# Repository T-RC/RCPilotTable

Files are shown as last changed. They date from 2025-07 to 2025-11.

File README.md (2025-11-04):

# RC Pilot Table
:airplane: This is a height adjustable, auto leveling table, intended for RC pilots. This table uses four [linear actuators](https://www.amazon.com/dp/B00NM8H67C/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) as legs.

:wheelchair: No crossmembers and a shallow deck make it usable for all pilots, including those using a wheelchair. 

:wrench: The table height adjusts simply via a rocker switch. It levels itself via a pushbutton. It is designed for outdoor use and runs on 2S-8S battery power.



## comments, questions and chat
You can leave comments, reviews, ask questions or start a conversation about this project [here](https://github.com/T-RC/RCPilotTable/discussions).

## Project background

Initially, I did not see an issue with the tables at my local AMA field. They are a common design, made of affordable materials and mostly construction wood. 



I believe the design is, at least in parts, inspired by prior art as featured [here](https://www.modelaviation.com/Club-Field-Safety-Benches).

One day, a fellow pilot pointed out that these tables are difficult for him to use. I realized that any table that has crossmembers connecting the legs is inaccessible for a pilot who uses a wheelchair. He also explained that a higher working surface would be nice to have. A few days later, I learned from another club member that a lower table surface would be better suited for his needs. I realized that a better table has to be height adjustable.
A web search for an off-the-shelf solution yielded no convincing options and neither did my search for better open source designs. I decided to come up with my own solution.

I chose to use [linear actuators](https://www.amazon.com/dp/B00NM8H67C/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) for the height adjustable legs. The rest of the design is driven by this decision. The actuators are marketed for use with solar panels, so they are weather resistant, IP54 rated, and affordable enough at around ~$50 a piece. They are however also not very precise, consistent or repeatable in their positioning and additional electronics are required for a level surface and to prevent rocking.

## The prototype
I have built one prototype so far. After it was finished, I donated it to the [Triple Creek Radio Control Aircraft Club](https://www.triplecreekrc.com) [(facebook)](https://www.facebook.com/share/1CnncBL3pf/?mibextid=wwXIfr) where it is in use since July 2025. The Tripple Creek RC field is located at 12705 Balm Boyette Rd
Riverview, FL 33579. 



## How to operate
Safety first: This is still a prototype. Stay clear of moving parts and use it at your own risk. Only plug in a battery while using it and be ready to unplug if anything unexpected happens. Don't leave a battery plugged in unattended.



The table has an internal 8-36V buck/boost power regulator, so it can handle anything from 2S to 8S battery. Simply plug your pack into the XT60 connector. I don't have exact numbers on the current draw, but obviously it will be higher for lower voltage packs. Very small 2S or 3S packs might not have enough punch.

Use the rocker switch to adjust the deck to the desired height, or slightly below it. Then use the leveling push-button and watch the magic happen. The table will attempt to raise the corners until the deck is level. Leveling happens upwards, so it's best to start below the desired height. The software code will time out after a few seconds, press the button again as needed. The programming is not very sophisticated yet. Press down on a corner and level it again if the table teeters.   

## How to build
A detailed build guide or a build video will follow if there is interest in it [(feel free to leave a comment here)](https://github.com/T-RC/RCPilotTable/discussions). For the time being, I an providing the [FreeCAD](https://www.freecad.org/) drawings, electrical schematics and STLs in the [subfolders](/drawings%20and%20images). I have video of the build of the electrical box. Github does not allow me to post it here, but I can make it available on request.

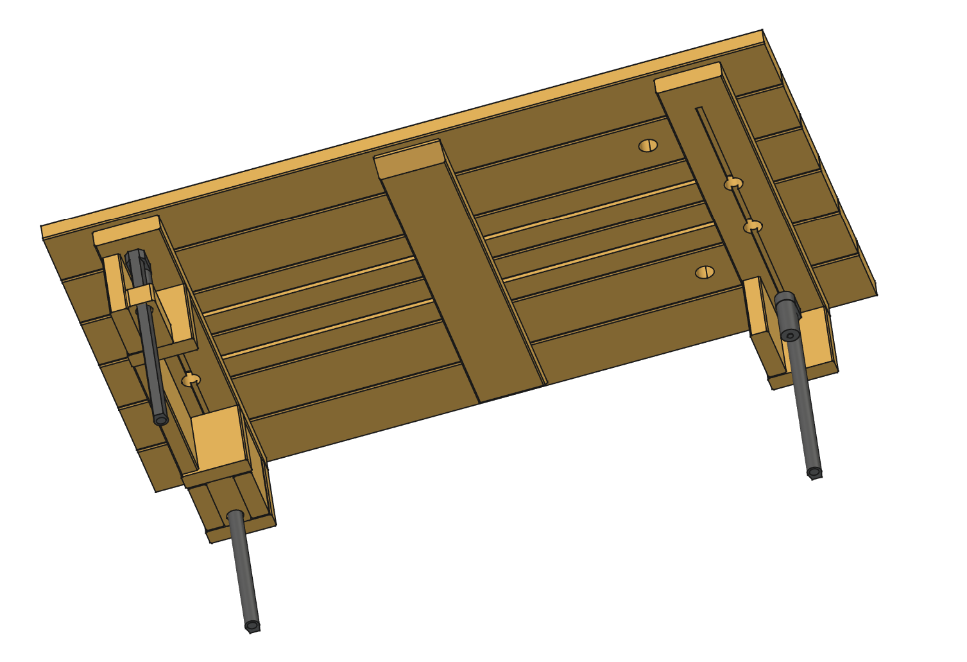
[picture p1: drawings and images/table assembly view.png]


### Lumber
I chose to only use one kind of timber for the entire build. This reduces waste and makes purchasing easier for us hobbyists. 2 in. x 6 in. dimensional lumber is readily available at hardware stores and local lumber yards. I built the first prototype from green western red cedar, but any hardwood or SPF will work the same depending on climate and weather, how long you want your table to last, how good you want it to look and how much $ you're willing to spend.

You need a total of approximately 50ft:

| count | length | use
| --- | --- | ----
| 6 pcs | 60" | for deck
| 3 pcs | 32" | for deck support
| 2 pcs | 15" | for side boards (optional, need to be fitted)
| 16 pcs| 6" | for the leg housing sides
| 4 pcs | 2"  | for the leg housing bottoms, use jig to cut

### Legs - linear actuators
The legs I used are [linear actuators](https://www.amazon.com/dp/B00NM8H67C/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) from Amazon.
### 3D Prints
I used [FreeCad](https://www.freecad.org/) for all the designs and [all drawings are here](/drawings%20and%20images). The STLs are posted [here](/3D%20print%20STLs). As filament, I am using either [Polymaker ASA](https://www.amazon.com/dp/B09DKQK318/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) or [Priline TPU](https://www.amazon.com/dp/B0BJ5XRDFB/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). 
### electrical box
I chose 3D-printing the box because I can skip several work steps and iterate faster this way. It also allows having a two colored front plate by stopping the printer and changing color after a few layers. An [off the shelve electrical enclosure](https://www.amazon.com/dp/B08N1DD5WJ/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) will work just as well though. As mentioned above, a build video is available.
### feet
The feet are 3D-printed in TPU at 100% infill.
### vertical wing restraint hanger
The vertical wing restraint is a removable design made from PVC pipe (not my idea, who get's credit?). It can be inserted into holes on the table to provide a hard stop for fixed-wing aircraft during setup and testing. Since these are not needed all the time, the restraints are removable and I designed a simple hanger to stow them when not in use.
The hanger is 3D-printed in ASA. I'm sure there is an injection molded substitute somewhere, but I couldn't find anything I liked so I designed my own.

### router template
This 3D-print is used as a jig to help cutting the bottom of the leg housing. The linear actuator has to be tightly held or else the table would get wiggly. Use [this template](/3D%20print%20STLs/Router%20template.stl) to hold and cut the wooden brackets.

### Amazon - what I bought
These are not affiliate links and I am not trying to monetize or profit of this project. Please also don't consider these reviews or recommendations. The Amazon link below simply takes you to a list of all the stuff that I personally bought and used during the build. It is not a comprehensive list either, but I think it might be helpful nevertheless.  

[Amazon list](https://www.amazon.com/hz/wishlist/ls/PGYE4HTR4F8?ref_=wl_share)

## What's next
- A full build video
- The software can still use some work.
  
let me know what you think [here](https://github.com/T-RC/RCPilotTable/discussions)

## See the prototype or learn to fly RC at Triple Creek RC
[website](https://www.triplecreekrc.com) 

[facebook](https://www.facebook.com/share/1CnncBL3pf/?mibextid=wwXIfr)

## License
Unless otherwise noted, this work is licensed under a
[Creative Commons Attribution 4.0 International License][cc-by].

[][cc-by]

[cc-by]: http://creativecommons.org/licenses/by/4.0/
[cc-by-image]: https://i.creativecommons.org/l/by/4.0/88x31.png
[cc-by-shield]: https://img.shields.io/badge/License-CC%20BY%204.0-lightgrey.svg

[][cc-by]

[cc-by]: http://creativecommons.org/licenses/by/4.0/
[cc-by-image]: https://i.creativecommons.org/l/by/4.0/88x31.png
[cc-by-shield]: https://img.shields.io/badge/License-CC%20BY%204.0-lightgrey.svg

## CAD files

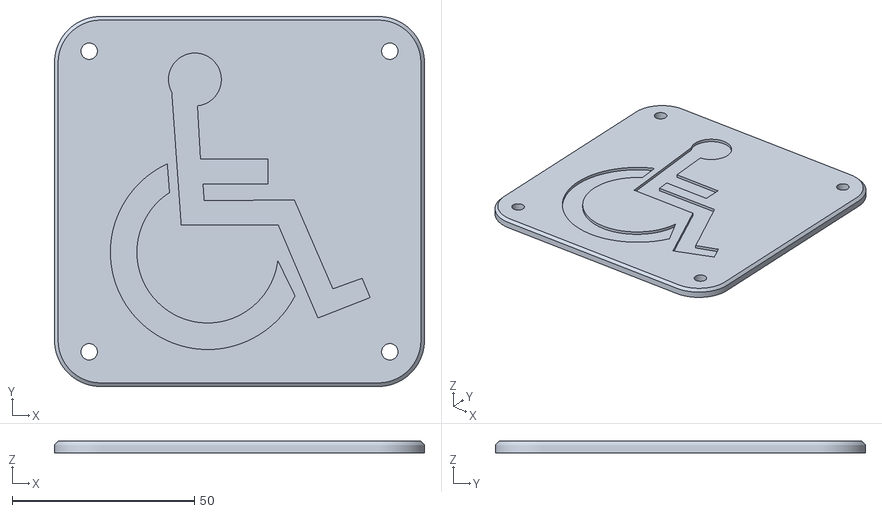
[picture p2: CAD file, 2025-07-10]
3D print STLs/disability sign.stl
101.6 x 101.6 x 3.17

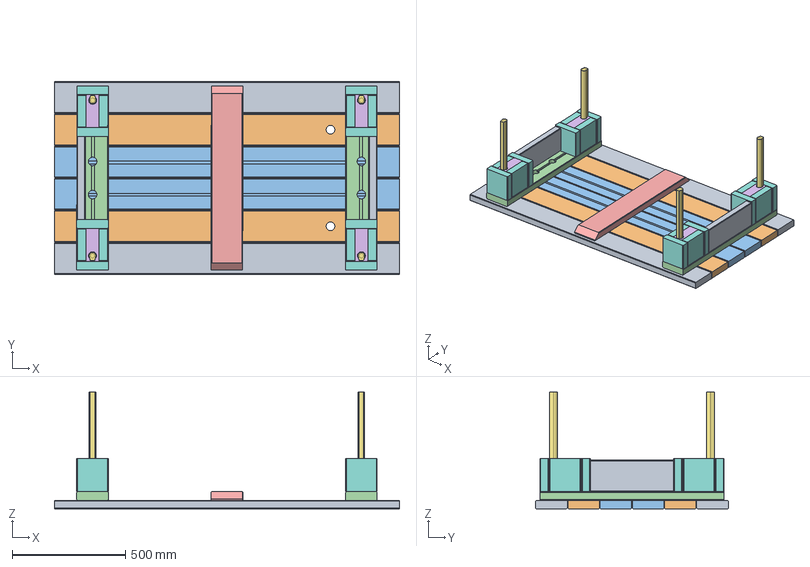
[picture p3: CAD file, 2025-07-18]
drawings and images/pilot table 037.FCStd
1524.0 x 851.4 x 516.3 mm
2x6 60" Deck x 2
2x6 60" Deck with holes x 2
2x6 60" Deck with groove x 2
2x6 32" SubDeck x 2
2x6 32" center SubDeck
2x6 scrap actuator adapter x 4
linear actuator body x 4
2x6 6" Leg x 16
2x6 15" sideboard x 2

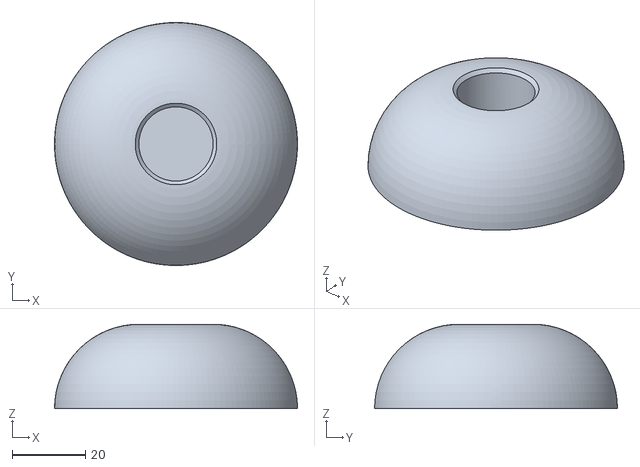
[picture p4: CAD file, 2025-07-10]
3D print STLs/pilot table foot.stl
66.2 x 66.2 x 23.0

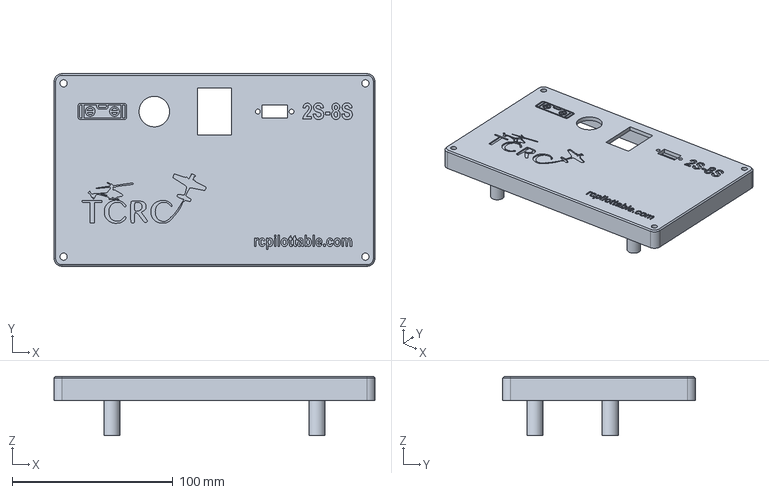
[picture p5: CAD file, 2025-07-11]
drawings and images/e-box 022.FCStd
200.0 x 120.0 x 37.0 mm

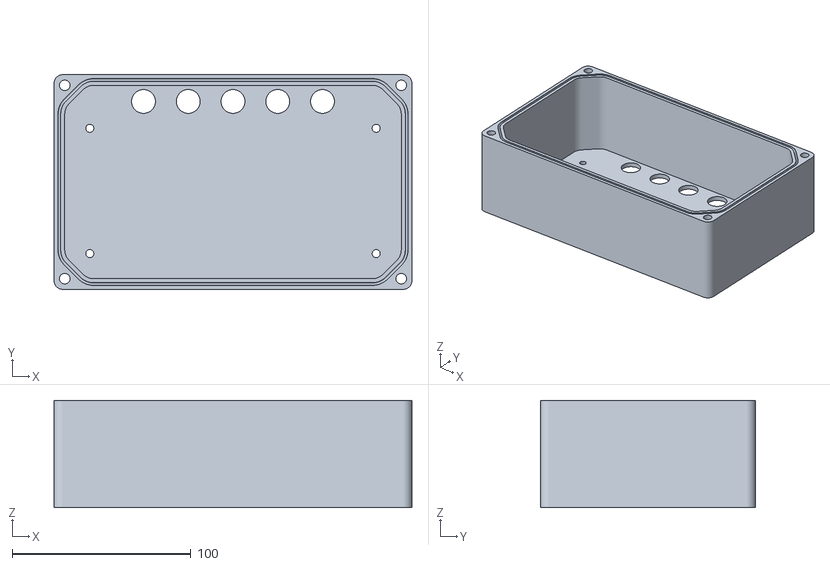
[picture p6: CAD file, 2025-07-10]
3D print STLs/e-box base.stl
200.0 x 120.0 x 60.0

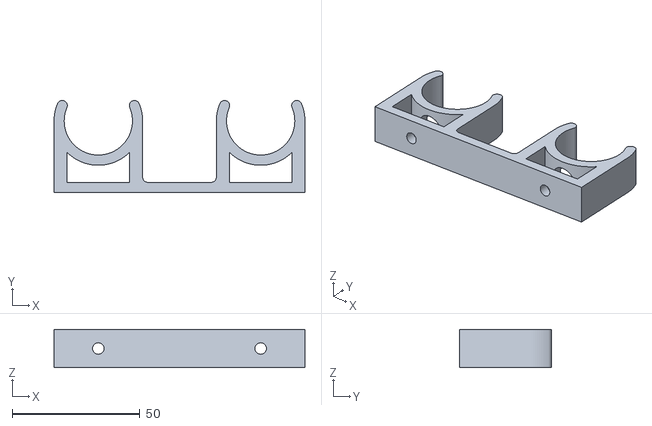
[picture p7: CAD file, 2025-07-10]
3D print STLs/PVC pipe stopper hanger.stl
98.2 x 36.0 x 15.0

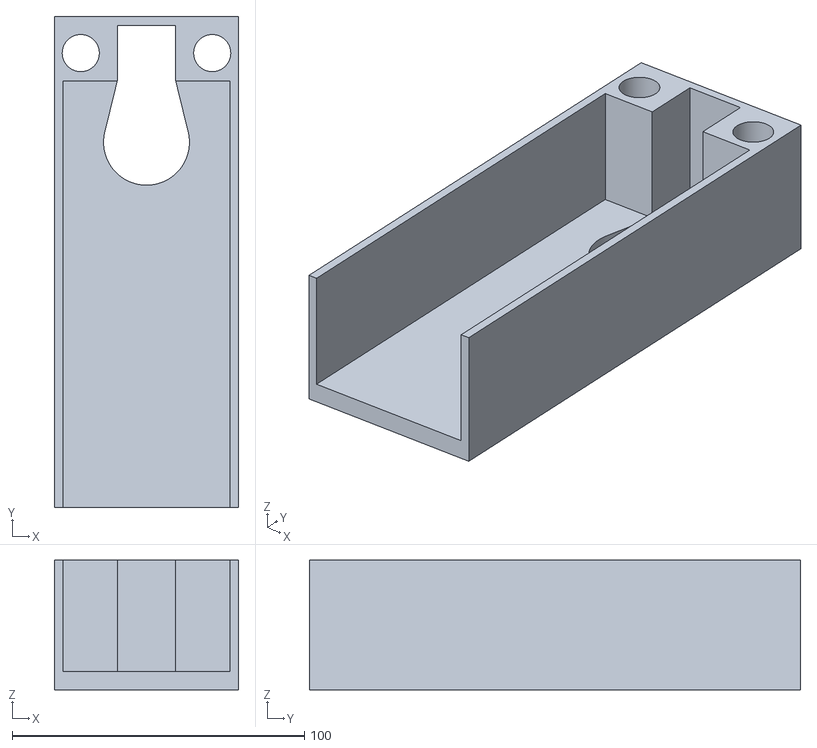
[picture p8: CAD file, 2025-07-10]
3D print STLs/Router template.stl
63.2 x 168.1 x 44.5

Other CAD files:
3D print STLs/e-box lid.stl

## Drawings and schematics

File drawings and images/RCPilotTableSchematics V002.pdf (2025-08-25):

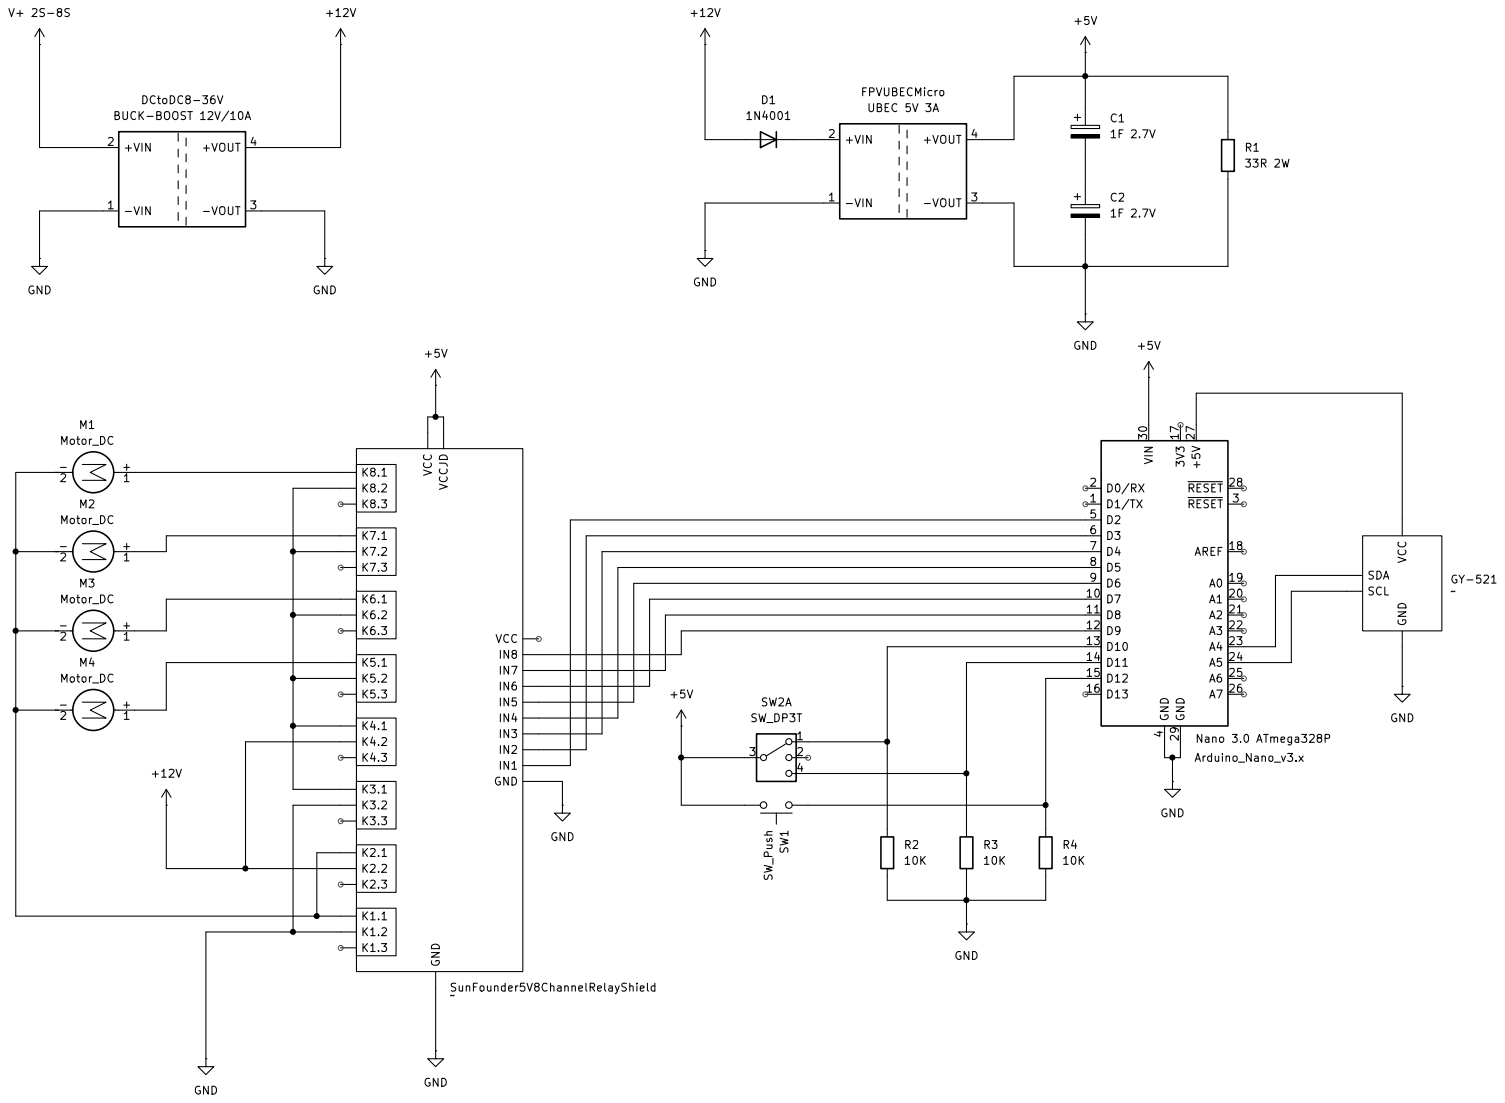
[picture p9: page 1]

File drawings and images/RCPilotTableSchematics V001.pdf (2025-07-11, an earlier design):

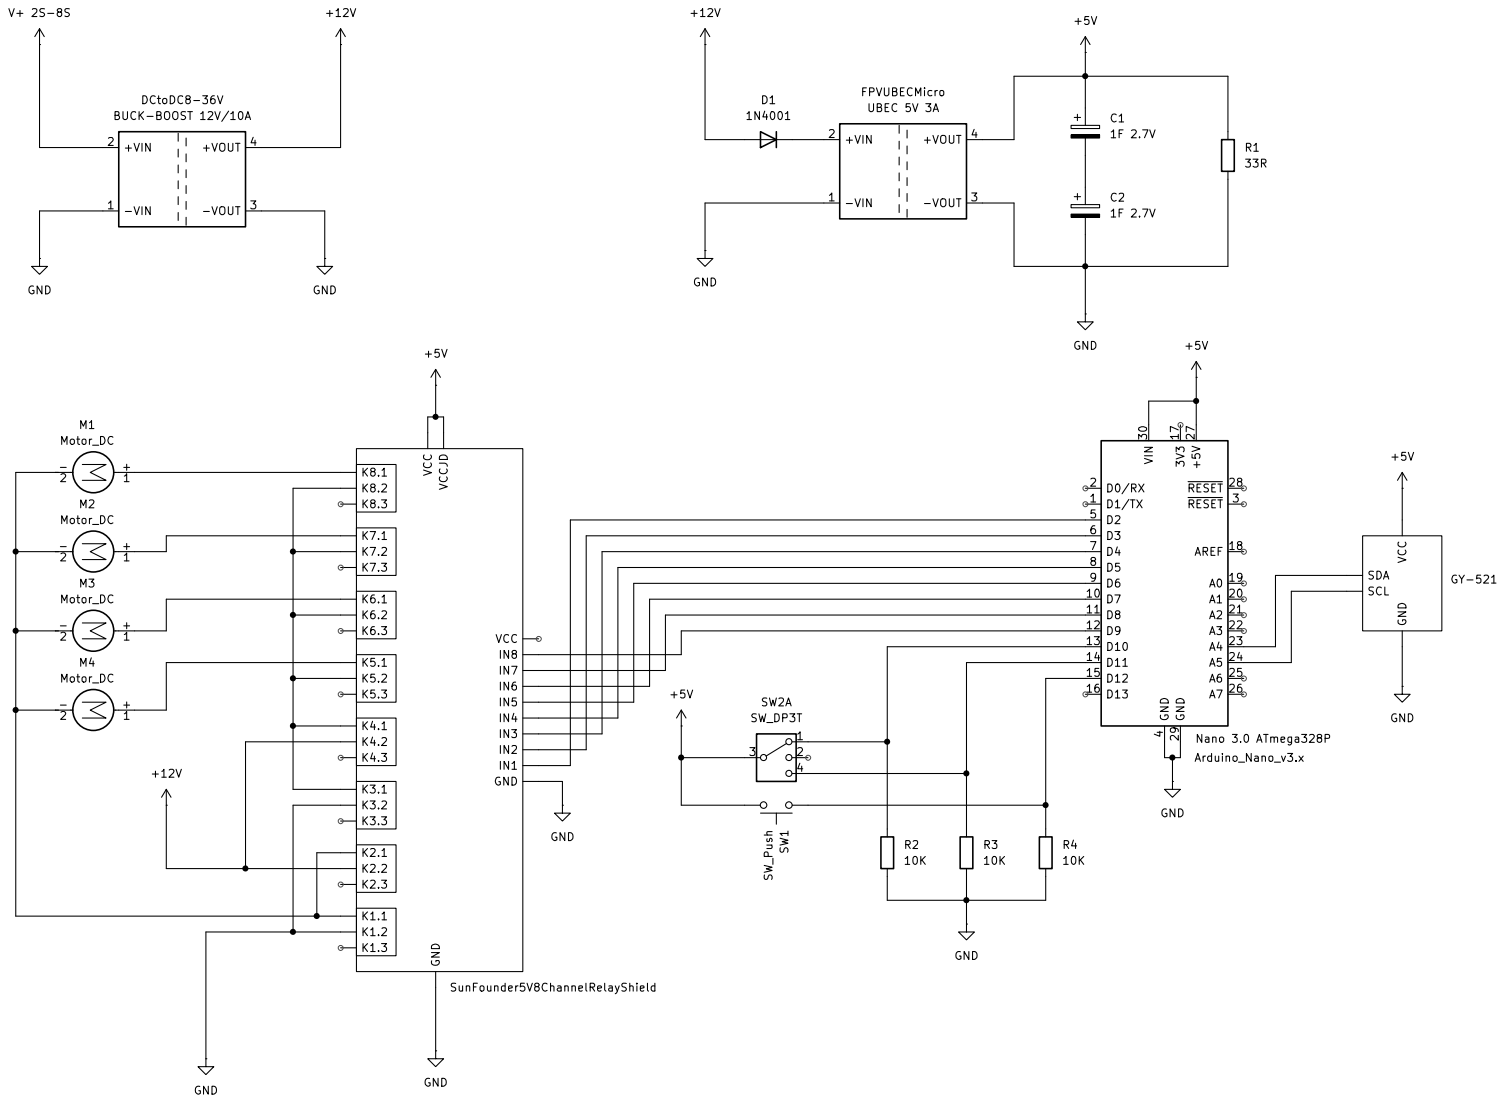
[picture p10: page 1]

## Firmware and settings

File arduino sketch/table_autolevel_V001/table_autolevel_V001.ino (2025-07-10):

// table leveling sketch
// 7 July 2025 T-RC

// libraries 
// wire comes as part of Arduino IDE
#include<Wire.h>

// define tags
uint16_t LevelingTimer = 0;   // leveling in progress when greater than zero
const int MPU=0x68;           // I2C address of MPU
int32_t AcX,AcY,AcZ,Tmp;      // raw accelerometer values from MPU
int32_t AverageX, AverageY;   // moving averages of accelerometer reads; to reduce signal noise
int32_t LevelWindow =  75;    // target accuracy of leveling; leveling stops once all legs are in range
double temperature;           // Temperature in Degrees C;
uint32_t counter = 0;         // to slow down serial data amount
int32_t X_Offset =  -400;
int32_t Y_Offset =  200;

// assign IOs
int UpButton    = 10;
int DownButton  = 11;
int LevelButton = 12;
int PwrRelay1   =  2;
int PwrRelay2   =  3;
int PwrRelay3   =  4;
int PwrRelay4   =  5;
int Motor1      =  6;
int Motor2      =  7;
int Motor3      =  8;
int Motor4      =  9;


void setup(){
// communication to MPU
Wire.begin();
Wire.beginTransmission(MPU);
Wire.write(0x6B);
Wire.write(0);
Wire.endTransmission(true);
//
// setup IOs
  // PushButtons
  pinMode(UpButton, INPUT);
  pinMode(DownButton, INPUT);
  pinMode(LevelButton, INPUT);
  // power reversing relays; HIGH means off!
  pinMode(PwrRelay1, OUTPUT);
  digitalWrite(PwrRelay1, HIGH);
  pinMode(PwrRelay2, OUTPUT);
  digitalWrite(PwrRelay2, HIGH);
  pinMode(PwrRelay3, OUTPUT);
  digitalWrite(PwrRelay3, HIGH);
  pinMode(PwrRelay4, OUTPUT);
  digitalWrite(PwrRelay4, HIGH);
  // motor relays; HIGH means power is off!
  pinMode(Motor1, OUTPUT);
  digitalWrite(Motor1, HIGH);
  pinMode(Motor2, OUTPUT);
  digitalWrite(Motor2, HIGH);
  pinMode(Motor3, OUTPUT);
  digitalWrite(Motor3, HIGH);
  pinMode(Motor4, OUTPUT);
  digitalWrite(Motor4, HIGH);
//
// open serial port for troubleshooting 
Serial.begin(115200);
}

void loop(){
  // prepare the MPU, read the data, calculate averages
  Wire.beginTransmission(MPU);
  Wire.write(0x3B);
  Wire.endTransmission(false);
  Wire.requestFrom(MPU,8,true);
  AcX=((Wire.read()<<8|Wire.read())+X_Offset);
  AcY=((Wire.read()<<8|Wire.read())+Y_Offset);
  AcZ=(Wire.read()<<8|Wire.read());
  Tmp=(Wire.read()<<8|Wire.read());
  temperature = (Tmp - 1600)/340 + 36.53;
  AverageX = ((AverageX * 95) + (AcX * 5))/100;
  AverageY = ((AverageY * 95) + (AcY * 5))/100;

  // process IOs
  // move up per up-button
  if (digitalRead(UpButton) == HIGH) {
    digitalWrite(PwrRelay1, LOW);
    digitalWrite(PwrRelay2, HIGH);
    digitalWrite(PwrRelay3, HIGH);
    digitalWrite(PwrRelay4, LOW);
    digitalWrite(Motor1, LOW);
    digitalWrite(Motor2, LOW);
    digitalWrite(Motor3, LOW);
    digitalWrite(Motor4, LOW);
    LevelingTimer = 0;
  }
  // move down per down-button
  else if (digitalRead(DownButton) == HIGH) {
    digitalWrite(PwrRelay1, HIGH);
    digitalWrite(PwrRelay2, LOW);
    digitalWrite(PwrRelay3, LOW);
    digitalWrite(PwrRelay4, HIGH);
    digitalWrite(Motor1, LOW);
    digitalWrite(Motor2, LOW);
    digitalWrite(Motor3, LOW);
    digitalWrite(Motor4, LOW);
    LevelingTimer = 0;
  }
  //intiate leveling per level-button
  else if (digitalRead(LevelButton) == HIGH) {
    digitalWrite(PwrRelay1, LOW);
    digitalWrite(PwrRelay2, HIGH);
    digitalWrite(PwrRelay3, HIGH);
    digitalWrite(PwrRelay4, LOW);
    LevelingTimer = 50;
  }
  // level the table
  else if (LevelingTimer > 0) { 
    if (AverageX >= LevelWindow) {digitalWrite(Motor1, LOW); } else { digitalWrite(Motor1, HIGH); }
    if (AverageY >= LevelWindow) {digitalWrite(Motor2, LOW); } else { digitalWrite(Motor2, HIGH); }
    if (AverageX <= -LevelWindow) {digitalWrite(Motor3, LOW); } else { digitalWrite(Motor3, HIGH); }
    if (AverageY <= -LevelWindow) {digitalWrite(Motor4, LOW); } else { digitalWrite(Motor4, HIGH); }
    LevelingTimer--; 
  }
  else { // turn off power, all motors, and reset all level flags if nothing else is happening
    digitalWrite(PwrRelay1, HIGH);
    digitalWrite(PwrRelay2, HIGH);
    digitalWrite(PwrRelay3, HIGH);
    digitalWrite(PwrRelay4, HIGH);
    digitalWrite(Motor1, HIGH);
    digitalWrite(Motor2, HIGH);
    digitalWrite(Motor3, HIGH);
    digitalWrite(Motor4, HIGH);
  } //end of IO processing

  //send troubleshooting data to the serial port
    if (counter % 10 == 0) {
      Serial.print(counter);   
      Serial.print("\t"); Serial.print(digitalRead(UpButton));  
      Serial.print("\t"); Serial.print(digitalRead(DownButton));  
      Serial.print("\t"); Serial.print(digitalRead(LevelButton));
      Serial.print("\t"); Serial.print(LevelingTimer);
      Serial.print("\tX = \t"); Serial.print(AverageX);
      Serial.print("\t Y = \t"); Serial.print(AverageY);
      Serial.print("\t Temp(C) = "); Serial.println(temperature);
    }

  counter++;
  delay(50); // end of loop - slow down processing to not overload the MPU and relays
} //end of void loop

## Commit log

2025-07-10 STLs
    upload 3D print STL files
    [PVC pipe stopper hanger.stl, Router template.stl, disability sign.stl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]
2025-07-10 animated
    animated table legs
2025-07-10 arduino sketch
    arduino sketch
2025-07-11 drawings
    additional drawings , first upload
    [e-box 022.FCStd, pilot table 035.FCStd]
2025-07-18 updated drawings
    [pilot table 035.FCStd, pilot table 037.FCStd]
